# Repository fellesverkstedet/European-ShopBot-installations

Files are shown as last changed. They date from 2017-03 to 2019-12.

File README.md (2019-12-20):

# European ShopBot installations

### The case

* Large format milling machines need special installation to be certified for public use in european countries
* Most Fab Labs and other community workshops have funding and operational restraints that require EU regulations to be followed

### Our goals

* Increase chances of Fab Labs and other community workshops making government approved installations
* Generally lower the threshold for people worldwide to make safe and pedagogic installations of large format milling machines.
* Avoid doublework in mapping out European rules for shopbot use
* Develop methods that keep machine operators in contact with the machines. Our goal is to help people learn and master tools and technology. [Jinba ittai](https://en.wikipedia.org/wiki/Jinba_ittai) is a Japanese four-character compound describing unity of horse and rider

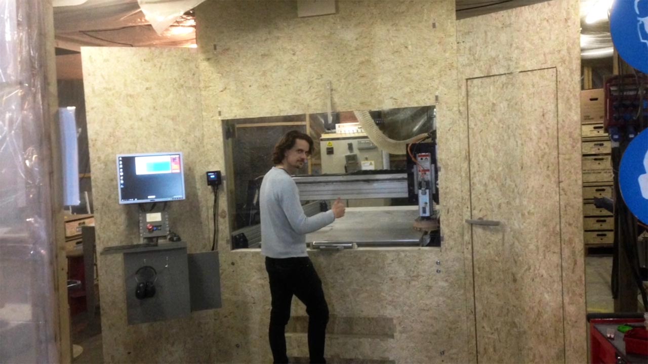
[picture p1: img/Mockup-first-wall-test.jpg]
Mockeup test
	
*1:1 mockup for testing function and ergonomics of current design*

### The solution in a nutshell

* Put a door/window or other physical barrier between the ShopBot and ShopBot operator
* Put a safety switch/senor on the door so that the ShopBot will stop if the room is entered

### Current issues

**#1** Some of the ShopBot electronics are not CE approved. Safety switch to the room must completely kill power. Killing power makes it neccessoary to re-home X, Y and Z axis after every entry.

Solutions we are exploring:
* **Stage 1** Add permanent Z homing plate and end stop on Z axis up direction. This way we can add to our post-processors a homing routine for all axes before each job. *(similar to using most 3D printers)*

We are evaulting the following workflow:

1. You place the material on the bed and insert your bit.
2. You close the door and power is enabled to the machine
3. You load the job without zeroing anything. The first lines of the ShopBot code coming out of your fusion/v-carve/mods/bark beetle post processor includes the following zeroing routine:
4. Z axis up until end stop hit *(end stop for Z needs to be retrofitted)*
5. Regular home X Y with end stops
6. Probe Z on a permanently fixed Z zero plate next to the bed
7. You get prompted to start the spindle and press OK
8. Job runs. You follow through the window and though the live feed on the camera inside the skirt
9. Job ends with the machine driving to the back and you enter the room.

Good thing is that we will never have to remind people to Zero X, Y and Z again. Bad thing is people need to learn to work with Zero point underneath the material and specify correct material thickness (you kind of need to get this right anyway though). The shopbot control software needs to  restart every time you you have opened the door. But rebooting the software is quick, and a small price to pay for not having to use the Z plate manually. It is still possible to jog the machine around, as long as the doors are closed.

* **Stage 2** Potentially find a way to not have to kill power to all axes when entering the room. Demands swapping electronic components and possibly the controll software

**#2** Putting the operator outside the ShopBot room reduces the feeling and controll and insights into the machines operation.

Solutions we are exploring:
* Have a short as possible distance between the front of the machines and the user/control panel.
* Use big windows
* Make a super fast, yet safe, autaomtic sliding door that opens with a button press. *(train door style)*
* Have a camera with live feed from inside the dust skirt
* Have a microphone with live feed
* Visualize various sensor data: Sound, vibrations, temperature, power consumption motors, power consumption spindle

**#3** Building garage size shopbot installations with external contractors is expensive

Solutions we are exploring:
* Make open plans Fab Lab operators can download and fabriate on the ShopBot itself. Doors, window frames, wall, ceilings, accoustic panels, camera dust skirt etc.
* Make clear 2D drawings that can be used as for faster project mangagemment and planning when setting up new Fab Labs
* Compile a bill of materials (BOM) of components that meet EU regulations

### Why is the ShopBot dangerous

* Spinning bits can shatter and start fire
* Moving mass can pinch
* Fine dust particles can contaminate lungs
* Loud noise can damage hearing

### The accessories that ShopBot offer

* Handlebars with switches *(apparently not enough to make the machine EU approvable)*
* Keypad for remote controll

### General EU rules

### Country specific rules

### Extreal resources and links

### Current solution *(WIP)*

* External switch for Z axis can be connected to input 5 on the ShopBot controll board. Can be read by ShopBot part files/scripts
* The file [XYandZzero.sbp](./ShopBot-config-files/XYandZzero.sbp) runs the an automatic homing routine. It was created by combinging a Shopots Home X Y script, Shopbots Zero Z script and move Z to custom end stop script by Dana Swift.
* [XYandZzero.sbp](./ShopBot-config-files/XYandZzero.sbp) first Zeroes X Y, then moves the head to the specified location of a fixed Z zero plate, than runs the Z Zero routine on the fixed plate and finsihes with moving the Z axis up to maxium position
* [XYandZzero.sbp](./ShopBot-config-files/XYandZzero.sbp) needs to placed in the C:\SbParts folder
* You need to modify the post processor of your CAM program to have this as the first line: **FP,C:\SbParts\XYandZzero.sbp**
* [ShopBot_AutoHomeXYZ_Arc_MM_Spindle_Control.pp](./post-processors/v-carve/ShopBot_AutoHomeXYZ_Arc_MM_Spindle_Control.pp) is an example of a modified PostProcessor for V-Carve
* Custom1, Custom4 and Custom10 are scripts that can be convenient for experienced machine operators. Example: press C+4 on the keyboard to run Custom4, it will bring the machine to a convenient location for manual toolchange

Files are set up and tested and used at your own risk. Be carefull!

Lines to edit for custom setup:
* Line **399**: Change value to so that Z zero will be at top of sacrafacial layer.
* Line **152**: Set the coordiantes of the center of your fixed Z zero plate

### Known bugs

ShopBot moved too fast at one point
* Turning power off to the ShopBot control cabinet, then quickly back on within about 5sec, seem to corrput the speed settings
* Closing the Sb3 application and resarting is reccomended if power has been off the control cabinet

V-Carve does not autmatically adjust home start and end Z height when working with Z zero point bellow material
* But you will get a warning if Z home height is bellow safe Z height. Solution can be to allways have a high Home Z. Can be safe if a Z proximity switch is fully functional.

### To do

**Technical**
* next. make permanent homing plate - DONE.
* make and test mount for z switch - DONE
* fix wiring of z prox switch and z zero plate - DONE
* aquire and test offical ShoBot poximity switch *(current test switch is cheap and unrelibale in heavy dust environment)* DONE, works well on Z axis
* make Z proximity switch stop the Z axis when moving up DONE
* aquire and test offical elctricty braker for sliding doors
* place zero plate in back of machine? reverese homing routine?
* find definate couse of speed error
* make spindle start automatically?
* do general user testing - testing so far is very postivie
* make shopbot software auto close and restart upon connection loss?
* make a previewer program that can preview toolpaths easily and automatically start and close SB3?

**Signage**
* Make overview of signage required in different countries
* Make and add vector files in this repo of grphics that can be replicated in a lab

**Documentation**
* Make info more overvieble
* Make BOM *(Bill of materials)*
* Collect and add external links

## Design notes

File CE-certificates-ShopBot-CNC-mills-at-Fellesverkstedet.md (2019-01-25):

# CE certificate ShopBot CNC mills at Fellesverkstedet

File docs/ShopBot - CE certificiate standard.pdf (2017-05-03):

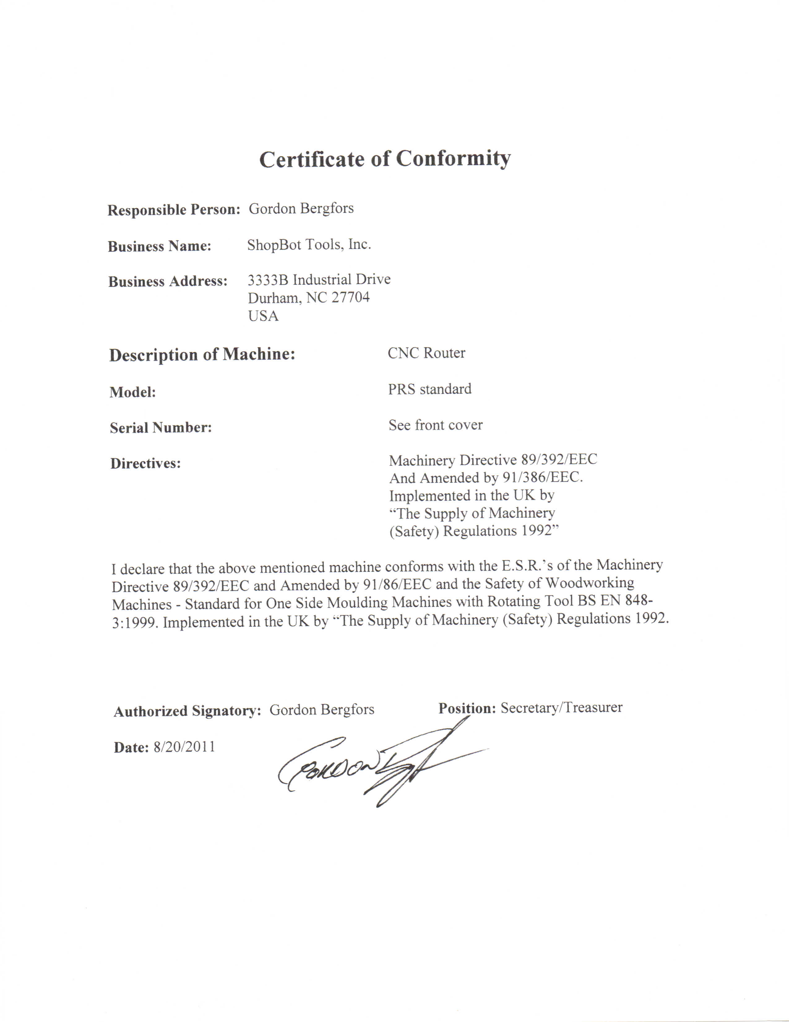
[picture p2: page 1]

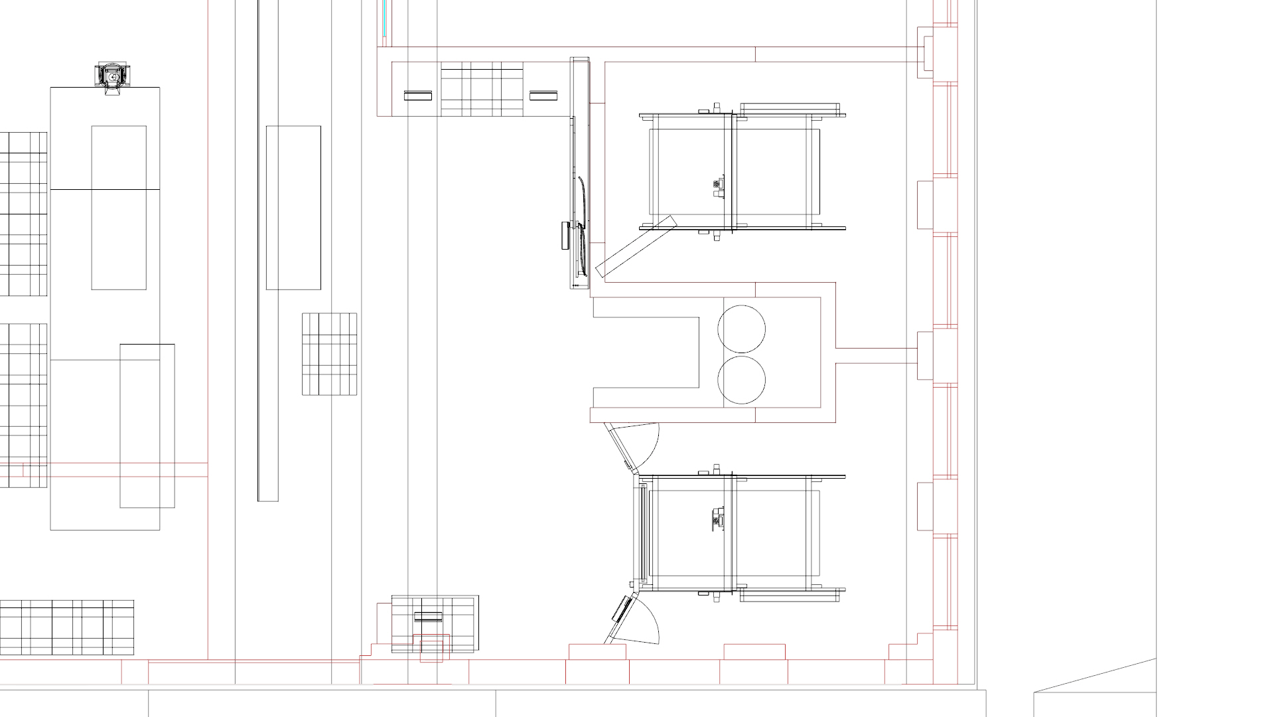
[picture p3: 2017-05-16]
img/ShopBot-optimzed-door-sketch-top-view.jpg

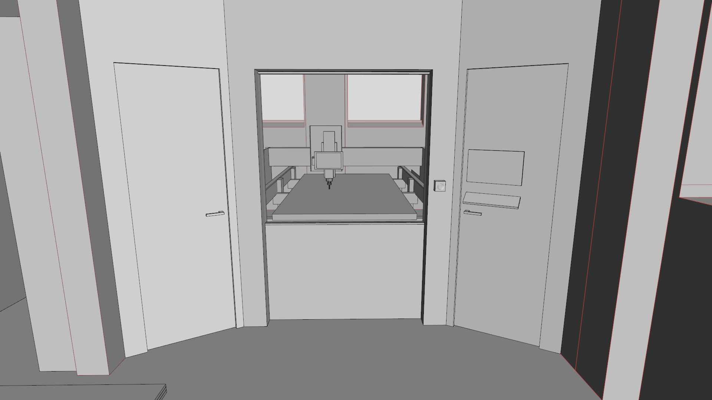
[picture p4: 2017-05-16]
img/ShopBot-optimzed-door-sketch-closed.jpg

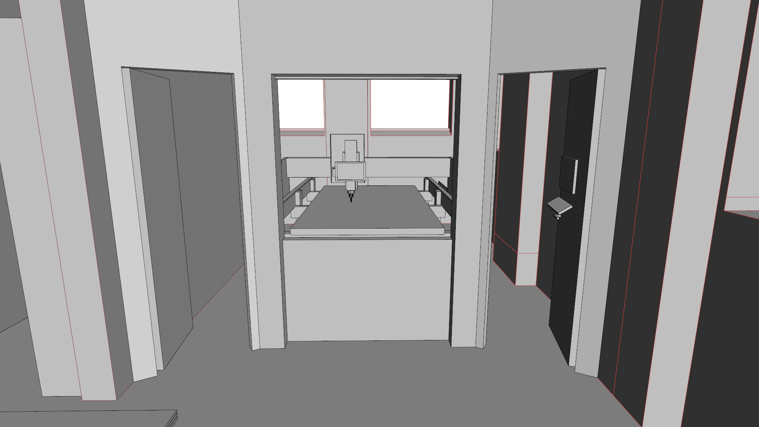
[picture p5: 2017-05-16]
img/ShopBot-optimzed-door-sketch-open.jpg

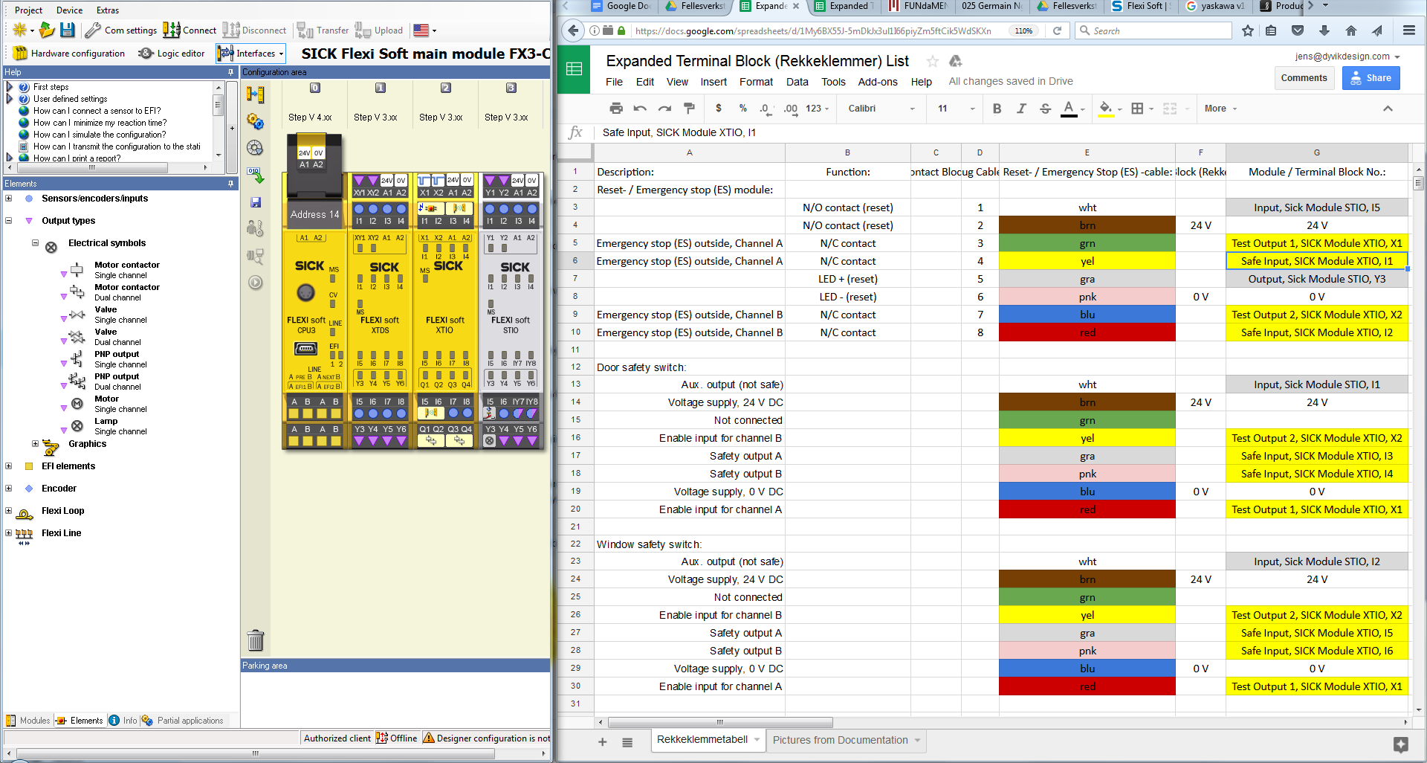
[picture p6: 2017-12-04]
img/Sick safety module programing.png

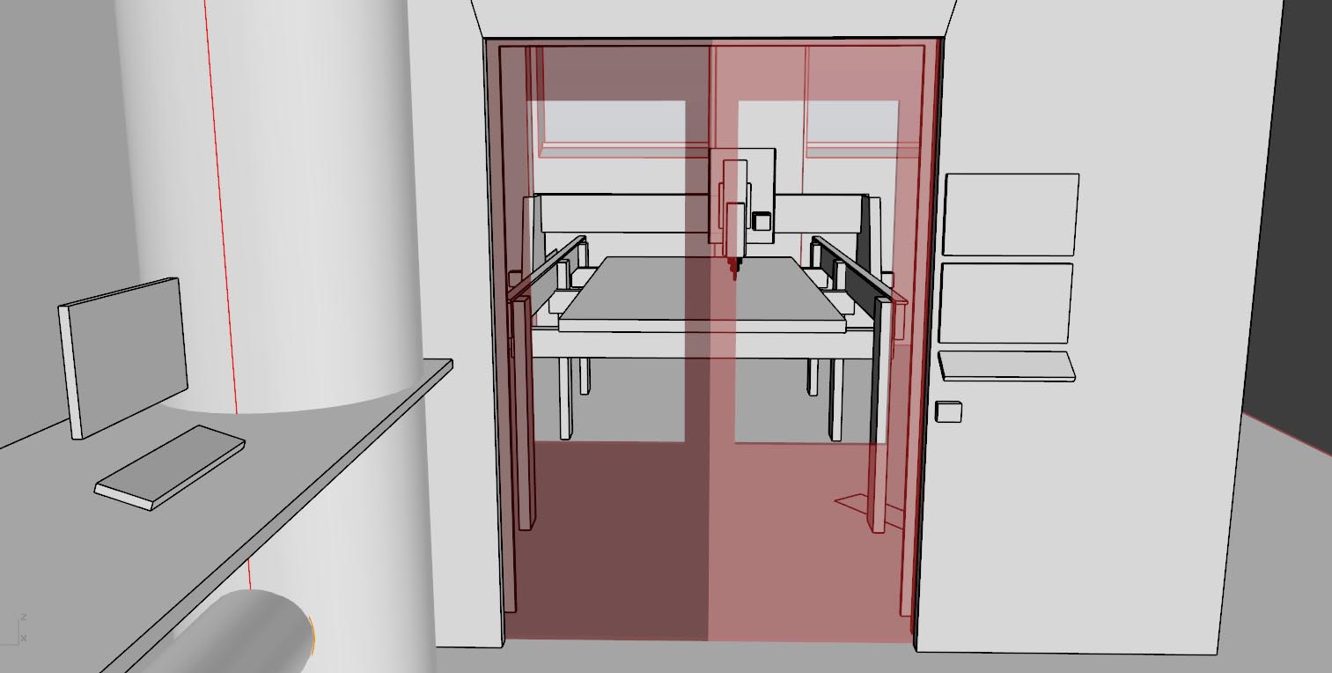
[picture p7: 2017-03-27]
img/ShopBot-safety-door-sketch.jpg

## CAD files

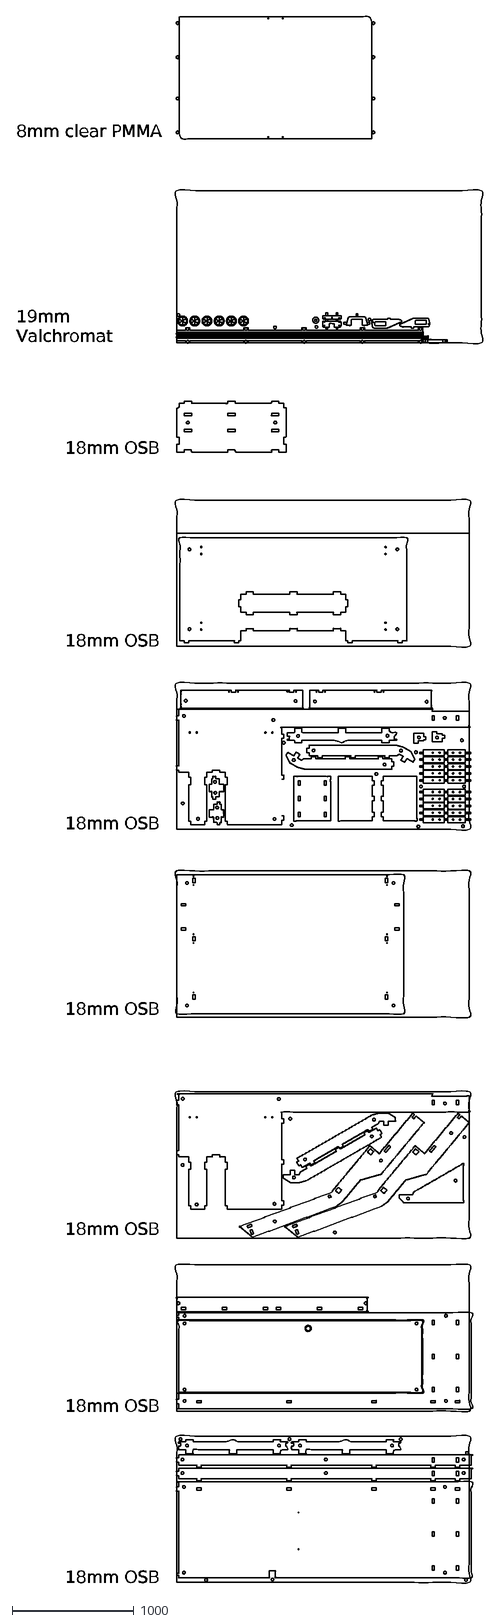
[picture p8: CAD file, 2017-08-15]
ShopBot-room-front-wall-cutsheets.dxf
18mm OSB
19mm Valchromat
8mm clear PMMA

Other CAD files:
Zprox-bracket-and-Zzero-plate.3dm
Zprox-mount-cnc-10mm-aluminium.3dm
safety-window-constuction.3dm

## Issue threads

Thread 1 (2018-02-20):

sudden stops in XY zeroing routine cause imprecision

Madouc, 2018-02-20:
currently the XYzero routine causes the stopbot to execute a sudden stop as soon as the endstop is reached.

however, if the physical endstop is not located right behind the sensor, there should be space to come to a ramped stop.

the ON INPUT command allows for a ramped stop by using the second parameter ( &TrgtHIT in the xyzero routine)
This should however only be used on the big-moves as you want to have a precise (repeatable) stopping point with the small moves.

Ramp-down should be adapted to stay within the end-stop detection.
Or after a big-move, the detection-interrupt could be adapted to only trigger when the carriage moves off the endstop.
(this would allow for moving on to the endstop without triggering a stop)

JensDyvik, 2018-02-22:
Great. Thank you for good input. I will test implement a ramped down big move. On our 96-48 alphas we have only about 10mm between the proximity switch trigger point and physical endstop to allow maximum work area and space for probing the bit on a probing plate. I am curious to how much travel we will need for a decent ramp down from high speed jogging. Will report back.

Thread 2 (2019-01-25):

Meeeting notes 25.1.2019

JensDyvik, 2019-01-25:
### Done
- Started work on CE certificate document

### To do's

Jens:
- Construct safety windows
- Mount sensors on windows and doors
- Wire safety electronics in bot2
- Make schematic of electronic wiring

James:
- Make map of safety documents
- Make roadmap
- Have risk analysis meeting

### Notes on schematic of electronic wiring
- Introduksjon/Innholdsfortegnelse  *(Introduction / Index)*
- Fordeling *(Inntak: hvordan kommer spenningen inn på anlegget? Beskrivelse av type spenningssystem etc.)*
- Hovedstrøm *(Effektkretser, normalt 230 / 400 V, -det som driver de store tingene som f.eks. motor)*
- Styrestrøm *(Normalt 24V, alt under 50 V DC og 120 V AC)*
- Arrangementstegning *(forenklet 2D skisse av fysisk plassering i tavle/styreskap)*
- Rekkeklemmetabell / Klemmliste *(Rekkeklemmer brukes i utgangspunktet for å skille mellom intern- og ekstern kabling inn i tavlen)*
- Kabelliste *(type kabel, info om skjerming og jord, dimensjonering [mm2])*
- I/O-liste *(Innganger- og utganger på PLS'en (Programmerbar Logisk Styring))*
- Parameterliste *(evt. dekket i SICK-autogenereringsdoku'en)*
- BOM-Liste *(Bill of materials, evt. dekket i SICK-autogenereringsdoku'en)*

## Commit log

2017-04-06 Added CAD sketch for Z zero plate and prox switch
    Also tweaked XYandZzero script
    [Zprox-bracket-and-Zzero-plate.3dm]
2017-04-07 Updated tweaked homing script
    [Zprox-bracket-and-Zzero-plate.3dm]
2017-04-24 Twekaed XY and Z homing script
    Also improved v-carve post processor. Now there is no uneccesary jog to
    home at beggining of a job
2017-05-16 added mounting bracket for inductive limit switch
    [Zprox-mount-cnc-10mm-aluminium.3dm]
2017-05-16 updated homing script to work with inductive proximity switch
    also added variables at begginging of script to simplify settup and
    tweaking
2017-08-15 added CAD file of first front wall test
    CNC milled from 18mm OSB sheets and 8mm clear PMMA
2017-08-15 Added cutsheets for first 1:1 test
    [ShopBot-room-front-wall-cutsheets.dxf]
2017-12-04 Improved vcarve post proessor
    Now with automatic material thickness compensation in homing routine
2017-12-04 Improved scripts for homing routine
2019-01-10 started work on high quality linear window
    [safety-window-constuction.3dm]
2019-01-25 Started work CE document
    to be completed during spring 2019
2019-04-09 added refined drawings of safety window with rails
